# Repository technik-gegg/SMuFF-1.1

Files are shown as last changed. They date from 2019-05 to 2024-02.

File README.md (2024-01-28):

# Welcome to the SMuFF project

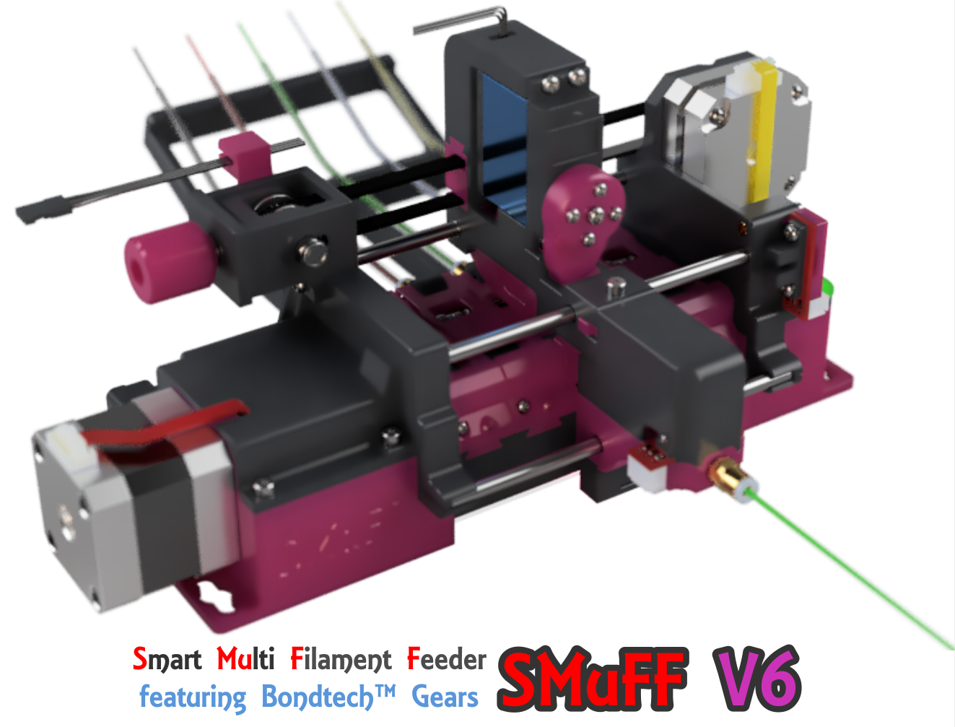
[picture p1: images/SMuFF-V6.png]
The SMuFF


Here's the official firmware package for the **S**mart **Mu**lti **F**ilament **F**eeder, as published on [Printables](https://www.printables.com/de/model/194737-smuff-v6-smart-multi-filament-feeder-with-bondtech) and [Thingiverse](https://www.thingiverse.com/thing:3431438). Read the full story on how it came to life on my official [SMuFF homepage](https://sites.google.com/view/the-smuff/).

If you like this project and find it useful, you may consider [donating](https://sites.google.com/view/the-smuff/downloads/assembly-manual#h.m5ewgcp0jfk6).

To use this firmware, you have to [compile it](https://sites.google.com/view/the-smuff/how-to/tutorials/compile-the-firmware?authuser=0) and flash it to one of these (already supported) controller boards:

| Board |  |
|---|-----|
| Bigtreetech [SKR mini E3 V3.0](https://www.biqu.equipment/products/bigtreetech-skr-mini-e3-v2-0-32-bit-control-board-for-ender-3) |**recommended** |
| Bigtreetech [SKR mini E3-DIP V1.1](https://www.biqu.equipment/products/bigtreetech-skr-e3-dip-v1-0-motherboard-for-ender-3)||
| Bigtreetech [SKR mini E3 V2.0](https://www.biqu.equipment/products/bigtreetech-skr-mini-e3-v2-0-32-bit-control-board-integrated-tmc2209-uart-for-ender-4) ||
| Bigtreetech [SKR mini V1.1](https://www.biqu.equipment/collections/control-board/products/bigtreetech-skr-mini-v1-1-motherboard-32-bit-arm-equipped-with-tmc2208-v2-1-tmc2130-spi-driver-stepstic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)||

The Bigtreetech SKR mini series boards are very small and yet powerful because of the 32-Bit STM Microcontroller Unit.

Of course, this firmware can also be configured to run on any other controller board, as long as it meets the specifications. Although you might be able to utilize older 8 bit boards, I don't recommended it - you'll most probably run out of memory (Flash/RAM) very soon. I recommend using a 32 bit controller board instead.
Make sure your board of choice has at least **256K** of Flash memory, **48K** of (S)RAM and all other components needed, which are at least:

+ two stepper motor drivers (sockets)
+ two endstop connectors
+ one servo connector (or two spare I/O pins for Software-I2C)
+ an onboard SD-Card
+ one spare serial port (USB or TTL)
+ a 128 x 64 pixel display connector
+ a rotary encoder connector

Simply create a new build environment in your **platformio.ini** and adopt the settings according to your controllers hardware in your custom **pins.h** file.

The configuration files **\*.json** and **debug.txt** have to be copied into the root folder of your SD-Card for the controller board. Hence, changing runtime parameters doesn't require recompiling the firmware. Just edit the settings from within the built-in menus or the [WebInterface](https://github.com/technik-gegg/SMuFF-WI), save them and reboot.

I've added the option to run GCode scripts for automated testing of your hardware.
In the **test** folder you'll find some sample scripts. Copy the folder over to your SD-Card and pick a script from within the menu to start the test run. Once started, the test will run infinitelly until you stop it.
Each test result will be displayed on the LCD and also sent to the log serial port (which is the USB port, if not defined otherwise).

For more information about building the SMuFF and some more detailed stuff, head over to my official [SMuFF homepage](https://sites.google.com/view/the-smuff/) or to my [Discord server](https://discord.com/invite/BzZ3rBf).

 

---

## Credit where credit is due

A special thanks to the folks who have created the following (Arduino) libraries, on which the SMuFF firmware builds upon:

+ [Adafruit](https://github.com/technik-gegg/Adafruit-PWM-Servo-Driver-Library.git) for the PWM Servo library
+ [Benoît Blanchon](https://github.com/bblanchon/ArduinoJson.git) for the Arduino JSON library
+ [Bill Greinman](https://github.com/greiman/SdFat) for the SD-Card library
+ [Oliver Kraus](https://github.com/olikraus/U8G2_Arduino.git) for the U8G2 display library
+ [teemuatlut](https://github.com/teemuatlut/TMCStepper) for the TMC-Stepper library
+ [the creators of the](https://github.com/technik-gegg/SoftWireSTM32/) SoftWireSTM32 library
+ [Tom Schimansky](https://github.com/TomSchimansky/CustomTkinter) for the Custom Tkinter Python package
+ [Akash Bora](https://github.com/Akascape) for the CTkMessagebox and CTkToolTip packages

---

## Recent changes

**3.25** - minor fixes/changes

+ restricted scanning of the I2C bus to valid slave addresses (0-7 and 120-127 are reserved addresses). Although this didn't cause any error yet, it could have caused some unwanted effects in the future.
+ added a new option to route debug messages to other than the default Serial 2 (a.k.a. TFT-Header): Create a file in the root folder of the SD-Card named:
  + **dbg2usb.txt** for Serial 0 (a.k.a. USB)
  + **dbg2exp.txt** for Serial 1
  + **dbg2oth.txt** for Serial 3

   **Keep in mind:** These files need no content. Not every port (except USB) is available on every board, it depends on board and configuration. To reset sending debug messages to default Serial 2, delete or rename the file.
+ added the **Adafruit Stepper + DC Motor FeatherWing** board as a 2nd option for the Spool-Rewinder controller. To use it, you have to define **USE_SPOOLMOTOR_FEATHERWING** in addition to **USE_SPOOLMOTOR** in the *config_defaults* and/or tick the according option in the *Firmware Build Configurator*.

**3.24** - added new "Firmware-Build Configurator"

+ made the build configuration easier by adding a custom dialog (Python/Ctk). Now, the *PROJECT TASKS* treeview only contains the basic build environments for each supported controller. Everything else can now be configured right after clicking on the **Build** task using this dialog:
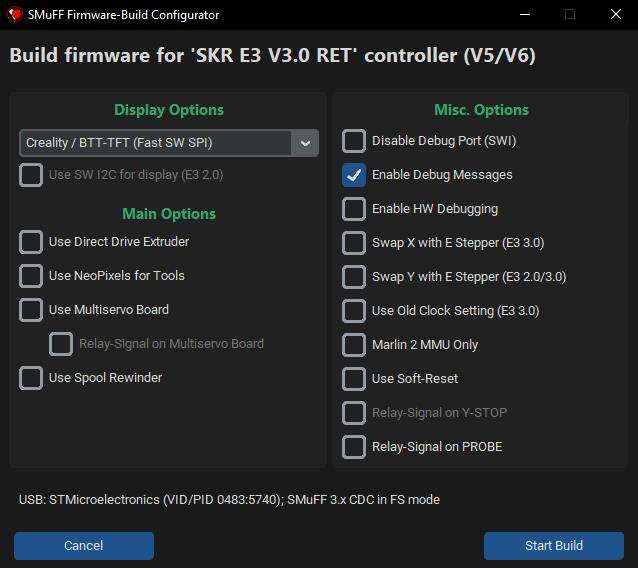
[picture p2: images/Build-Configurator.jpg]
Firmware Build Configurator

This is by far more convenient than parsing through the *platformio.ini* or trying to find the build environment you want.
Tooltips will show up when hovering over the checkboxes, which briefly explain why you would use this option.
After the build you'll find a **readme-build.txt** file in the output folder, listing the options that have been set for this particular build.
To define a set of **personalized default settings** depending on the controller used, one can list them under the *config_defaults* section in *platformio.ini*.
*Please be aware that for using this feature, PlatformIO needs to install some Python packages once. This happens automatically at your very first build.*
+ updated SdFat library reference to 2.2.0
+ added the option to use the "old" clock settings (those recommended by STM) for the SKR E3 V3.0 board instead of the new ones introduced in version 3.23.
+ added a couple more debug messages while the firmware is being initialized.

**3.23** - bugfix, Motorized Spool Rewinder option added

+ fixed the bug that caused some (newer) SKR E3 V3.0 boards not being recognized (enumerated) when connected via USB.
+ added **_SPM** build environments, which allow utilizing the [Motorized Spool Rewinder](https://sites.google.com/view/the-smuff/how-to/build/the-spool-rewinder). To use this option, you have to copy the *help* and *menus* folders to your SMuFFs SD-Card. Also, please notice the added content in **MATERIALS.json**.
+ added GCodes **M3**, **M4** and **M5** to allow controlling the spool motors of the *Motorized Spool Rewinder*.

**3.22** - reorganized Build Environments

+ reorganized Build Environments as announced in 3.21.
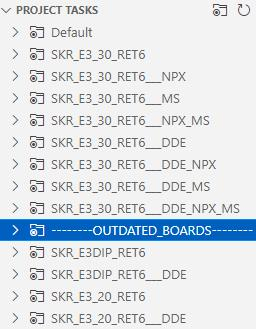
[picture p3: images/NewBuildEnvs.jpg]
New Build Environments
.
+ added include of <stdint.h> to SMuFF.h, since latest builds seem to fail.

**3.21** - some changes based on the previous release

+ reworked the Build Environments in **platformio.ini**
 Since the **SKR E3 V3.0** has become the most dominant contoller board and the others are getting more and more outdated, I've decided to get rid of some of the Build Environments for "older boards" and add all the possible permutations for the E3 V3.0 instead. The suffixes are meant to be self-explanatory but as a hint: **NPX** means NeoPixels (on tools), **MS** means Multiservo and **DDE** means Direct Drive Extruder.
 Here's what the *PROJECT TASKS* treeview in VSCode now looks like:
 New Build Environments
 Simply open the Build Enviroment that matches your setup and click on "Build".
 Outdated Build Environments are still contained in the ini-file but need to be un-commented in order to make them show up in the *PROJECT TASKS* treeview.
+ the (FYSECT / BTT / MKS) **MiniPanel 12864 V2.1** display has become the default option now. It's the cheapest and easiest to source display, so I declared it the "standard".
+ while playing around with the new behaviour of **USE_NUM_PIXELS** introduced in the previous release, I figured, it's far easier to have the number of LEDs configurable at runtime and thus, I've moved it to the SMuFF configuration file. Hence, this definition is now gone from the platformio.ini!
When you update to this version, please keep in mind to also copy the new **display.mnu** and **m205.txt** to your SMuFF's SD-Card, into the folders *menu* and *help* accordingly.
+ I also found an unpleasant but logical behavior in the *Marquee* animation when more than 7 LEDs are in use: It skips LEDs because on the beatsin() calculation and BPM settings, so I fixed that.
+ while I was at it, I also added two new Idle-Animations: Rainbow and Cylone. Thus, you need to copy the **anim-type.opt** to the *options* folder as well. Then pick the one that you fancy the most from the *Display menu*.

**3.20** - small feature change

+ corrected the behaviour of the **USE_NUM_PIXELS** definition in *platformio.ini*. This defines how many **NeoPixel LEDs** one plans to use for one tool (which usually is: "1 LED per tool").
This feature comes in handy when you're using a NeoPixel strip with a higher density. The "standard" NeoPixel strips come with a density of 60 LEDs/meter but they're also available in 30, 72, 96, 144, 240 or even 332 LEDs/m.
It turned out, that on strips with **144 LEDs/m** the LED spacing is around 7mm (i.e. 1000/144 = 6.94), which corresponds to 3 LEDs for 21mm! Coincidentally, this is also the exact width of one Filament-Guide. Hence, using a 144 LED/m strip saves you from the tedious job of cutting a strip and re-soldering the LEDs in order to get them into the right position. Simply use a longer strip (3 LEDs * number_of_tools) and set **USE_NUM_PIXELS** to 3 before compiling the firmware.

**3.19** - bug fix

+ fixed bug in Selector homing. When homed, SMuFF wasn't able to select tools because the Selector endstop was still triggering.

**3.18** - minor bug fix

+ fixed bug in displaying menu items

**3.17** - minor bug fixes / optimizations

+ fixed bug in platformio.ini for SKR Mini environment.
+ fixed bug in *NeoPixels on Tools*, if more than 5 tools are being used. Init of the NeoPixels happened before the Config was read and hence the count of tools/NeoPixels was incorrect.
+ optimized code for the steppers (*ZStepperLib*) yet again. The *isrStepperTimerHandler()* method now has an overall runtime of about **15uS** on a **STM32F1** MCU running at 72MHz.
+ changed some methods in timers.h/timers.cpp in order to shave off some microseconds in processing time.
+ fixed bug in synchronous movement of the steppers. Feeder stepper wasn't moving at the same pace as the DDE Feeder.
+ changed the USB signature to **STMicroelectronics SMuFF 3.x**. This way it's easier to distinguish which controller is for the SMuFF on the Raspberry Pi.
+ added meaningfull description headers to all methods in *ZStepperLib*, so it can be reused in other projects.
+ moved hardware Debug-Pin for E3-DIP controller from **Y-STOP** to **SWCLK** for a cleaner wave form. Since this is for my debugging only, you don't have to care much about this change.
+ removed TMC library and build flags from **E3-DIP** and **SKR MINI**, since those boards have no native TMC support (i.e. not being controlled through serial or SPI) and hence TMC drivers are running in "Standalone" a.k.a. "A4988" mode.
+ modified the **Acceleration Distance** behaviour. If this value is set to **0**, SMuFF will use 20% of the total distance for accel/decel, which results in a somewhat smoother acceleration/deceleration.
+ fixed bug stepper movement not stopping on endstop trigger. For some (still undiscovered) reason, the endstop ISR doesn't fire while steppers are moving.
+ changed/removed a couple of debug messages to make them a bit more meaningful.

**3.16** - bug fixes / enhancements / cleanup

+ **changed the stepper motors timer prescaler from 24Mhz to 2MHz** (internally 4MHz). This means, you **must** adjust your stepper ticks, otherwise steppers are going to turn terribly slow! Had to do this in order to gain more granular control over the stepper motors at lower speeds.
*Rule of thumb: Divide your current speed settings (Max. speed, Accel. speed, Purge speed, etc.) roughly by 10.*
The stepper timer in fact is running on double the frequency (4MHz) in order to achieve a longer pulse on the stepper driver, because now every 1st tick is used to set the STEP signal, every 2nd to reset the STEP signal. This makes the *Step-Delay* setting unnecessary and you should set it to 0. Though I left this setting in the config, just in case one needs it.
+ changed behaviour of "Unload retraction". If a value is set, it will only be executed if filament is fully loaded (down to nozzle). Keep in mind that this feature is used to shorten the filament remains when using the Cutter and yet only works on a Bowden setup.
+ changed data-type in *purgeFilament()* from uint16_t to double for more accurate purging.
+ changed the method of debug outputs in endstop interrupt functions, since sending data to serial ports from within ISR routines is always a bit critical and may block or crash the controller.
+ added **DEV4** debug flag for a more granular output control of debug messages (i.e. printing incoming GCodes, memory stats, ...).
+ updated GCode **M100** to determine free system memory (RAM). Before, this GCode only returned "ok".
+ added printing out memory stats every minute if *DEV4* debug flag is set.
+ removed the "*Mirroring the display on a VT-100 terminal*" feature introduced in V2.24 completely. Although it was nice to have back then, the software options around the SMuFF have evolved. Hence this feature is obsolete now and was only messing up the source code.
+ removed the (meanwhile) obsolete conditional code for FastLED library. My modified Adafruit NeoPixel library is covering all that's needed.
+ overhauled the code for handling the NeoPixels on tools. NeoPixels will not update as long as one of the stepper motors is spinning (Feeder / Selector), which makes the steppers run smoother.
+ added parameter **P** to GCode **M700** (load filament) in order to purge material (after it's being loaded). If no *value* (e.g. *M700 P*) is given, it'll purge the configured purge amount, otherwise the length of filament given in *value* (e.g. *M700 P12.34*).

  **[ Bug fixes ]**

+ fixed the bug that puts a "loading" dialog on the display while in *Testrun mode* (kudos to **palkovnik807**).
+ fixed the bug where retries were not being decremented while unloading filament (a.k.a "infinite loop" if unloading went wrong).
+ fixed a potential buffer overflow in *drawPurgingMessage()* and *printPeriodicalState()* functions.
+ fixed a bug that may have caused the MS1/MS2/MS3 pins being set up wrong on the **E3-DIP V1.1** (only), because the according pins on the MCU were in an undefined state. Now those pins are being set to LOW (0V) at startup.

**3.15** - minor changes / bug fixes

+ added option **NEVER_DISABLE_SERVOS** in *platformio.ini* section *'other'* which will inhibit disabling servos after they had been moved. The default behaviour is that the SMuFF will disable the PWM signal on **Wiper** and **Cutter** servos after wiping/cutting, because some servos run less jittery when disabled.
However, it turned out that disabling the PWM signal on some servos causes those servos eventually start moving out of the blue. Allowing the PWM signal to stay active helped fixing this issue.
If you discover random movements on your Wiper/Cutter servo, activate this new option before compiling the firmware.
*This option however doesn't influence the behaviour on the Multiservo board(s) - which still are the better option for driving servos.*
+ fixed the bug that sometimes caused the filament not being fully retracted (i.e. Feeder endstop not triggered). Happens only if the configured "Bowden length" value doesn't match the real distance or the filament "slipped" during retraction. In such case the Feeder was supposed to retry until the endstop has triggered but didn't due to wrong condition checking. Thanks to **palkovnik807** on Discord for pointing it out.
+ fixed the bug that caused the **DDE Feeder** not doing a purge under certain conditions because the stepper wasn't enabled. Thanks to **Thyom** on Discord for finding it.
+ added printout of DDE Feeder endstop state for GCode **M119**, in case SMuFF is configured for DDE.

**3.14** - minor changes / bug fix

+ added option **USE_NUM_PIXELS** in *platformio.ini*. Usually, the number of Neopixels matches the number of tools but in some special case you may have more Neopixels on your strip then tools. In order to make the animations using all pixels, enable this definition and set its value to the according number.
+ fixed bug where Lid servo didn't close before unloading when Cutter has been configured as sitting "on top".

**3.13** - Changes for Duet3D and Serial display / some bugfixes

+ fixed bug in TMC driver **Stealth-Mode setting** via SMuFF-WI. Value was accidentally inverted.
+ fixed bug that caused a compilation failure when using the *SKR_E3_30_RET6___DDE* build environment.
+ added [SMuFF-Backbone](https://sites.google.com/view/the-smuff/work-in-progress?authuser=0#h.m19pbkoy3v6p) schematic and PCB design.
+ added **DuetSerial** (port) setting to **SMUFF.json** and menus. You **must** now define the serial port where the Duet3D/RRF is connected to (set to Ser.1 by default). This serial port will only be taken into account if the SMuFF is configured for Duet3D/RRF. For this option you need to copy the modified **options.mnu** and **duet3d.opt** files into the according folders on your SMuFFs SD-Card.
+ added **DspSerial** (port) setting to **SMUFF.json**. The Display serial port can only be configured either through the **-D DISPLAY_SERIAL_PORT** definition in *platformio.ini* or manually in SMUFF.json but not from the menus (because there will be no menus in this mode). See notes on **USE_SERIAL_DISPLAY** for version **3.00** down below.
+ updated **M42** & **M280** & **M205** help files (for Multiservo use).
+ added Dialogs and Sound support on SMuFF-WI when *USE_DISPLAY_SERIAL* is enabled.
+ added **SWAP_SELECTOR_ENDSTOP** build option for those who experience the X-STOP (used for Selector) is not being triggered on a **SKR E3 V3.0**. With this option enabled, the firmware expects the Selector endstop to be connected to *Y-STOP* rather than *X-STOP*.
+ added *JAM* flag in periodical status messages; This is being used in my OctoPrint/Klipper plugins to indicate whether or not the tool change has failed for some reason.
+ added option to switch the *Debugger Serial Port* from within **debug.txt** on startup, without the need for recompiling the firmware. To use this option simply add a **;x** after the value, whereas *x* determines a port number between **0** and **3**. Port **0** always indicates the **USB** serial port, whereas ports **1..3** depend on the controller board you're using (*port 2 is the default value and is assigned to the **TFT** header on most boards*).
*Keep in mind:* This setting will vanish once you set the debug flags via GCode **M111** and store them using **M500**.
+ added option to switch the *Debugger Serial Port* on the fly via **M205** GCode. To use it, simply apply parameters **P"ChangeDbg" Sx**, whereas *x* is the number of the new serial port in the range of **0..3** (see description above).
*Keep in mind:* This setting is temporary and will be reset at the next boot.
+ added option to filter in help files. After the **?** append the phrase to filter for. For example: **M205?dist** will only show the header and all lines containing the string *"dist"*.

**3.12** - Changes for the MULTISERVO option

+ reworked **MULTISERVO** option. For one it's now named *USE_MULTISERVO* for more consistency throughout the other options. For the other, it's now being used to configure all servos to control them via an external board (Adafruit Multiservo/FeatherWing/ [SMuFF-Backbone](https://sites.google.com/view/the-smuff/work-in-progress?authuser=0#h.m19pbkoy3v6p) board). This external board is always being controlled by using software I2C. The pins used for SW-I2C vary throughout the different controller boards.
+ the **USE_MULTISERVO** flag will become more importance in the future, hence I moved that option to the *[other]* section of *platformio.ini*.
+ modified the external **SoftWireSTM32 library** which had a bug that caused that the library wasn't able to scan for devices on the I2C bus properly.
+ moved relay control pin on **SKR mini E3-DIP V1.1** from **MS3** pin of the Z-Axis driver socket (in DDE mode) to the **TH0** pin if the **USE_MULTISERVO** flag is set. This is because this signal is being used as the data pin (SDA) for the software I2C controlling the Adafruit Multiservo board.
+ added **USE_MULTISERVO_RELAY** flag to the compile options in order to control the relay via output #5 on the Multiservo board instead of *MS3*, *TH0* or *PROBE* pins. This will be the future method of controlling the relay switch. **Please notice:** This method requires a pull-up resistor of 4.7K - 10K, either on +5V or +3.3V to make the signal switch as intended. The reason being is that the outputs on the Multiservo board are configured as open-drain.
+ corrected build environment for **SKR mini V1.1** (FastLED library was still referenced instead of the Adafruit Neopixel library).
+ fixed the bug that caused the **SKR mini V1.1** to hang at startup (wrong *debugSerial* port has been initialized).
+ added a couple more meaningful error messages to the GCode interpreter.
+ changed **SERVOMAP.json** config file to reflect the new MUTISERVO options. Please copy this file over to your SMuFF's SD-Card.
+ changed **ServoMinPwm** and **ServoMaxPwm** settings in SMUFF.json. These settings work better with the Multiservo boards. Copy the modified file over to your SMuFF's SD-Card and don't forget to reconfigure your servo angle settings.
+ added the two user controlled servo ports (USER1/USER2) to **M280** GCode and **M42** GCode when using the MULTISERVO option. Send M280 P1000 / P1001 if those ports are supposed to drive custom servos, or M42 P1000 / P1001 if those ports are configured to be used as output pins (i.e. to be switched on/off).
+ added **M260** GCode to allow scanning for I2C devices at runtime using the GCode interface.
+ updated some of the KiCad files to KiCad version 6.x

**3.11** - Some minor changes

+ added flashing of the "Periodical State sending" glyph on the display when it's enabled. Flashing happens at half the frequency of states being sent.
+ added current relay state (**E** / **I**) to "Periodical States".
+ changed output of **M122W** and **M503W**. *M122W9* and *M503W0* are now sending all state/configuration data at once, which makes SMuFF-WI connect faster.

**3.10** - Some minor changes / bug fixes

+ **removed SKR E3 V1.2** from the list of supported devices because this board isn't optimal for the SMuFF V6. Consider moving to E3 V2.0 or better E3 V3.0.
+ changed some default settings in *SMUFF.json* which fits better for V6 default configuration.
+ switched from FastLED to AdafruitNeoPixel library throughout for all boards.
+ fixed bug where DDE extruder wasn't reading out the endstop while retracting.
+ fixed bug with NeoPixel refresh.
+ added dedicated timer for NeoPixel refresh because the existing solution interfered with servos and steppers.
+ (re-) added timer for servos because the existing solution interfered with the stepper timer.
+ changed timer priorities and intervals to get rid of servo jitter.
+ changed priority on timers, so the stepper timer (and thus the stepper movement) is a bit more agile now.
+ added GCode command **M155** for fast switching of *sending periodical status messages*.
+ GCode **M205 help file** updated.
+ cleaned up *platformio.ini* by extending environments in *__DDE.
+ added GCode command **M562** to reset a *Feeder Jam* remotly.
+ added more status/error responses in order to make the Klipper module run smooth
+ added feeder states (SPL in periodical states) for all variants. This value is now (lower nibble: Splitter, upper nibble: non-Splitter):
  + 0x00 means *not loaded*
  + 0x01 means *loaded to Splitter*
  + 0x02 means *loaded to Nozzle*
  + 0x10 means *loaded to Selector*
  + 0x20 means *loaded to Nozzle*
  + 0x40 means *loaded to DDE*
+ added "JAMMED" state on display when feeder is being jammed

**3.00** - Moving from Maple to Arduino Core STM32 framework  

+ ported firmware from **Maple** to new **Arduino Core STM32** (stm32duino) framework in order to make boards with different MCUs available. This version is still compatible with the predecessor SKR controller boards, such as the SKR Mini/E3-DIP/V2.0.
+ added **debug.txt** to define the amount of debug messages being spit out without re-compiling the firmware. Also added the option of changing the debug level through GCode, which is **M111**. See *M111?* for details.
+ compiling the firmware without the **-D DEBUG** option will now reduce the memory footprint drastically. Although, removing debug messages completely will make your first setup much harder, so handle with care.
+ updated help files in *help* folder.
+ reduced the number of build environments in *platformio.ini*. Please note that **USE_DUET3D** has become obsolete and is now a runtime option. However, the **USE_DDE** flag still is the same and hence it's got its own build environment (*\*___DDE*).
+ added build options summary when compiling. This makes checking the build options you've set a breeze:
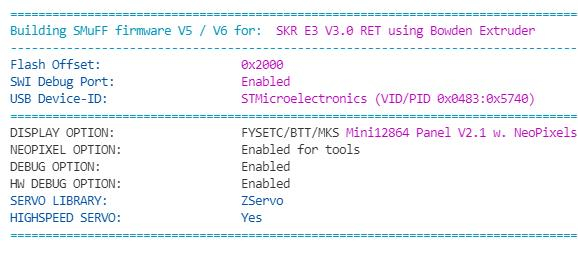
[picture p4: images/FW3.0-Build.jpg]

+ removed Servo-Timer. Servos are now served through the *General Purpose Timer*, which makes the servo timing more percise and thus the servos less jittery.
+ added flag **MIMIC_LIBMAPLE_USB_ID** in order to keep the USB ID compatible for use with my [OctoPrint plugin](https://github.com/technik-gegg/OctoPrint-Smuff). This setting is default for the "old" SKR E3 controller boards but not for newer boards.
+ added flag **SWAP_SERVOS** which will assign the Lid and the Cutter servos to the BL-Touch header for SKR E3 V1.2 / V2.0 / V3.0 (it swaps Wiper and Cutter servo signal pins).
+ added new build environment for **SKR E3 V3.0** controller board. This board has been fully tested and is ready to use.
+ added new build environment for **SKR E3 RRF** controller board. **Not tested yet!**
+ added **SyncSteppers** flag in SMUFF.json, which, if turned on, synchronizes movement of two or more steppers, so that they start and finish at the same time. Set by default.
+ eliminated code for *ZPortExpander* completely.
+ restructured **Options** menu on the display. Copy the new *options.mnu* file to the SMuFFs SD-Card (folder menus).
+ added **USE_SERIAL_DISPLAY** option for future use. ***Please be aware:** By setting this flag, no display code will be compiled into the firmware and hence the only way to control it is by using the WebInterface.*
+ added **USE_FAST_SW_SPI** build option for Creality  displays (or compatibles such as the BTT TFT). This allows you to simply connect the display through EXP1/EXP3 with the applied 10 pin cable, and still get a decent speed and responsiveness on the display.
+ added a couple of new STL files for Inlet-Guides and new SKR housing. Inlet-Guides are now available for 5 and 7 materials (thanks to maker **Defenc**). For a different amount of materials on the Inlet-Guides, please download the according [STEP file from Thangs](https://thangs.com/mythangs/file/55305).
+ fixed bug which caused the SMuFF to hang after showing the main menu.
+ refactored some code from **SMuFFtools.cpp** into *DisplayTools.cpp*, *SoundTools.cpp* *ServoTools.cpp* and *TerminalTools.cpp* for better maintainability.

---

**2.44** - Addition for alternative RRF boards

+ added inverting option for the *Busy* signal that goes to a endstop of a RepRap Firmware board (other than the Duet3D). This was needed since some of the alternatives might not be able to trigger upon the original signal. To use this option, you'll also need to copy the updated **options.mnu** file to the *menus* folder of your SMuFFs SD-Card.
Basic instructions for setting up a RRF (Duet3D) board can be found [here](https://sites.google.com/view/the-smuff/how-to/tutorials/configure-the-duet3d?authuser=0).
+ removed old code that might have disturbed Duet3D signals.
+ fixed a typo in the folder name which caused the E3 V1.2 version not being able to build correctly.
+ reorganized *Build Environments* in platformio.ini. This change allows you to pick some of the build options quickly. In the *Project Tasks* you'll now find different environments named after the controller board (i.e. **SKR_E3_12** for the SKR E3 Version 1.2) and three with the same name plus an extension named either **DDE**, **DUET** or **DDE+DUET**. The one without an extension is the "basic" version (no DDE, no Duet3D). **DDE** builds the firmware for the DDE option, **DUET** for the Duet3D (a.k.a. RRF) and **DDE+DUET** for a combination of both of the previously mentioned options. Thus, you don't have to mess with these settings in the [options] / [extruder] section anymore (the latter section has become obsolete now).
Keep in mind that you still have to set the correct **display** option before you build the firmware, in case you're using something else than the DIY display.
+ added **M118** GCode to enable you to send text (GCode) from the SMuFF/WI console to a specific serial port. Parameters are the same as for Duet3D/RRF fimrware, whereas **P**x defines the serial port, and **S**"..." defines the message to send. Please update you *help* folder with the latest files.

**2.43** - added new STLs

+ added new STL files for the small servo carrier. Please read [the instructions posted here](https://sites.google.com/view/the-smuff/work-in-progress?authuser=0#h.ssx9ayceh6f4).
+ updated version number to make the version check in WebInterface happy again.

**2.42** - some minor bug fixes/changes

+ made contrast setting a live function (contrast of the display will change as you rotate the knob, which makes it easier to set up).
+ corrected contrast setting after reading configuration on startup.
+ changed backlight color order on *FYSETC Minipanel* from GRB to RGB.
+ added SKR E3 RRF board to the collection. **This is experimental only and will not compile due to the lack of support for STM32F4 in some libraries. Do not use!**

**2.41** - some fine tuning on recent changes

+ added **DebugFreq** setting to **SMUFF.json** which allows to set the frequency (in Hz) applied to the hardware debug pin for testing purposes. This value can be changed during runtime via M205 GCode as well.
+ defined Duet3D signal pins (*DUET_SIG_FED_PIN* and *DUET_SIG_SEL_PIN*) to be on thermistor pins (THB and TH0). Because of the R/C filter on those pins signals are limited to a max. switching frequency of **100Hz**, which is sufficient for this purpose.
+ removed redundancy in display includes throughout all the Pins.h files. These are now located once in *Display/Display.h*.
+ corrected some pin defintions in all Pins.h files.
+ revived the SKR Mini V1.1 board (because it's still available and in use).

**2.40** - code reorganization and bug fixing

+ removed old boards, such as ESP32, SKR Mini, FYSETC AIO II, mainly because they're discontinued and just mess up the project.
*Because of this change the version number is now 2.4*
+ removed code for ESP32 entirely. As long as the ESP32 has such a deficit on I/O pins, it's not feasible as a SMuFF controller.
+ split up **Pins.h** to disentangle the confusing code for display pin definitions. Now each display type has it's own *DSP_xxx.h* header file and the initialization takes place in the according *Display/xxx.h* file instead of *SMuFF.cpp* and *SMuFF.h*.
+ reorganized code in order to reduce memory footprint and allow compiling for NeoPixels unconditionally. Due to usage of the PortExpander (PCF857X), which only purpose was to extend the amount of I/O ports on the ESP32, the memory footprint exploded. It's corrected now and the memory (RAM) footprint is slightly around 35% instead of 86%!
+ corrected pinout for standard RepRap display and FYSETC 12864 Minipanel on E3 V2.0 board.
+ improved drawing speed on the DIY OLED display for E3 V2.0 board.

**2.34 - 2.39** - skipped versions

**2.33** - bug fixing for DDE option

+ fixed a bug that caused stalling on the DDE stepper motor while purging because of wrong settings.
+ added more frequent status information for the WebInterface while swapping tools.

**2.32** - added Cutter position for DDE option

+ **moved main repository on Github to SMuFF-2.0 branch. No need to download from the SMuFF-2.0-(Experimental) anymore.**
+ added **CutterTop** option in SMUFF.json which was needed for the latest Orbiter-Extruder mod. For the Orbiter-Extruder you need to set this option to *false* because the Cutter sits below the DDE.

**2.31** - added Cutter handling for DDE option

+ added purging of filament when DDE is being used in conjunction with the Cutter in order to release the 2nd endstop. To use this, set the **PurgeDDE** flag in SMUFF.json accordingly.
+ fixed bug in feedToEndstop which caused an abort if the *InsLen* parameter was set too low.
+ added all **STL files** for V6 to this repository
+ added **Device** parameter in SMUFF.json. This string can be 15 charaters long and sets a distinct name for the current SMuFF device (i.e. the printer it is attached to). The name of the device will be show up in the WebInterface and also in GCode **M503**. This name can only be set/changed through the WebInterface or directly in the config file but not in the menu.

**2.30** - DDE option added

+ added **USE_DDE** flag in platformio.ini. Set this flag if you intend using the SMuFF on a Direct Drive Extruder. Further instructions you'll find on the [SMuFFs website](https://sites.google.com/view/the-smuff/how-to/tutorials/set-up-a-dde).
+ added new menu items in **options** menu for DDE. *Please notice:* The Use DDE flag can't be switched during runtime, it's only shown to indicate whether ot not this firmware was compiled for DDE.

**2.29** - Some critical changes, Splitter option added

+ **Critical:** Moved pin for **switching the relay** from *PROBE* to the *MS3* pin of the Z-Axis stepper driver for E3-DIP boards. This was needed since the PROBE pin sometimes has a problem delivering a valid signal for the relay board. If you still encounter problems switching the relay, try adding a 10K pull-ip resistor between +5V and the signal pin MS3.
+ added some minor changes to improve the communication with the [WebInterface](https://github.com/technik-gegg/SMuFF-WI).
+ fully integrated the Splitter option.
+ added new **main-menu** variant for the Splitter option.
+ added Splitter option settings in **options** menu.
+ extended **M700** and **M701** GCodes to handle Splitter option. A suffix **S** loads unloads to/from Splitter, whereas a  **R** suffix in M701 allows you to reset the currently saved states.
+ added feed states for Splitter option, which reflects if and to where the filament has been loaded. States will also get saved to EEPROM.json.
+ added new icon for the "fully loaded" state (in F2) on the main screen when using Splitter option.
+ fixed bug not turning display backlight back on after idle state.
+ set Servo min./max PWM to more conservative values of 900 and 2100. This might force you to tweak the Lid open/close positions on your SMuFF a bit. If you go below minimum and above maximum, this might cause your servo to overheat and eventually break (depends on the servo).
+ added software support for EStop MUX when using the "advanced" Splitter option. This feature is using the 2nd I2C (EN/STEP pins on Z-Axis steper driver socket) pins for communication if not compiled for the DIY/LeoNerd's display. On DIY/LeoNerd's displays it uses the 1st I2C, which also drives the display. To enable you to use this option, you'll need to compile the firmware with setting the **USE_SPLITTER_ENDSTOPS** definition in *platformio.ini*.

**2.28** - More bug fixing for WebInterface, added linear stepper support for Lid

+ fixed bug causing test GCode not being executed when initiated over [WebInterface](https://github.com/technik-gegg/SMuFF-WI).
+ added new periodical status infomration for TMC, SD-Card and LID.
+ changed the periodical status interval to 0.5 sec. when connected to the [WebInterface](https://github.com/technik-gegg/SMuFF-WI).
+ added option to compile for **V6S**, which is basically V6 but using a linear stepper on the Y-Axis (Revolver) for the Lid instead of a servo.
**Please notice:** *When using this option, the servo signals (Wiper & Cutter) come from the Z-Axis socket. Wiper signal moves to DIR pin, whereas Cutter signal moves to MS3 pin. That's because the STEP and EN pins are being used for the 3rd serial interface.*
+ added REVOLVERMAP.json to the configuration files, which defines the travel distance for the Lid linear stepper on each slot separately.
+ added materials (as in PLA, PETG, ...) to the materials definitions. Old "Materials" became "MaterialColors".
+ cleaned up code in GCode parser, saved a few bytes of Flash memory.

**2.27** - Bug fixes for WebInterface

+ corrected setting for "Speeds in mm/s".
+ corrected "Fan Speed" value validation (minimum was 1 instead of 0).
+ added synchronization with WebInterface when settings were changed locally.
+ set Heated Bed pin to 0 in init. So it won't turn on the heater MOSFET anymore.
+ fixed bug that caused the relay not switching when *useServo* was set to false.

**2.26** - Important changes

+ due to low memory on some boards, I had to split the **SMUFF.json** and relocate the steppers configuration into a separate file **STEPPERS.json**. Please make sure that you copy this new file to your SD-Card as well.
+ because of the same reason I removed the "Ser*N*Spd" setting in the SMUFF.json configuration file and replaced it for an array named "Baudrates".
+ changed **M205** GCode command and made all settings available. This way remote controlling it is way easier.
+ added some functions for the [SMuFF WebInterface](https://github.com/technik-gegg/SMuFF-WI) app.

**2.25** - Minor changes for Duet3D

+ modified the logic for interfacing with a Duet3D controller.
+ added **M577** GCode command to retrieve Duet3D signal pins status. Connection needs one additional wire from the SMuFF down to the Duet3D end stop input in order to do tool changes properly.

**2.24** - Minor changes

+ replaced all UTF characters in menus. Please copy all menu files onto your SD-Card and replace the old ones.
+ added a feature to mirror the display contents on a debug terminal (VT100 terminal emulation). This will only work on a controller board that has a *..RET..* MCU (because of the doubled memory) and if it's being enabled manually in the **SMuFF.json** config (**TermMenu** set to **true**).
**Please notice**: This feature was made for conveniance purposes (i.e. when you're connected to the debug interface having the printer/SMuFF out of sight). It's not meant to replace the display.
If this feature is turned on and when not in menus, the topmost line on teminal will replicate the information of the SMuFFs main screen.
+ corrected **Microsteps** options for TMC drivers.
+ removed I2C scanning when no IC2/TWI device is expected because the scanner is blocking the startup for a couple of seconds.
+ moved buzzer timer because it interfered with software serial library.
+ updated some help files.
+ revived loading sounds from SD-Card function. You can now modifiy all sounds to your personal flavor (see README.md within sounds folder for instructions).

**2.23** - Minor changes / bug fixes

+ added separate definitions for LED_TYPE and COLOR_ORDER for backlight and tool Neopixels.
+ changed name *servo* to *servoWiper* to avoid ambiguity.
+ changed **LED_TYPE** and **COLOR_ORDER** on **MINI12864 PANEL V2.1** because it turned out to be WS2811 not WS2812B.
+ changed **M206** to use floating point values for the Selector distance.
+ added checking for min. speed when using mm/s. Min. speed for Selector is about 5 mm/s because of the lower steps/mm. Feeder can go down as far as 1 mm/s.
+ fixed a bug in the calculation of speeds in mm/s. **However, I still recommend using speed settings in ticks rather than mm/s** (that's: SpeedsInMMs set to false). If you do use mm/s, please be aware that accelleration/decelleration are not being taken into account and therefore it's only a close estimation of the speed (which doesn't really matter for the function of the SMuFF anyway).
+ fixed bug for not initializing the software serial when not running on a SKR E3 2.0 board (which operates on a hardware serial).
+ added back setting the internal RSense on a TMC stepper driver when not on a SKR E3 1.2/2.0 board.
+ added software I2C support for LeoNerds OLED module (by GMagician). **Please notice**: If you get a compile time error stating *LeoNerdEncoder::begin(SoftWire\*)* has not been found, you have to delete the LeoNerd-OLED-Module-Library folder from the **.pio/libdeps** folder manually.

**2.22** - Changed configuration file names; Minor changes for FastLEDs

+ **IMPORTANT:** Configuration files must now have the **.json** extension, **not .CFG**! This was necessary because most people forgot to rename them and thus the SMuFF failed at startup.
*From now on, just copy the configuration files to the root of your SD-Card; no need to rename the files.*
+ updated Neopixel (FastLED) functions / animations.
+ added **Anim. BPM** and **Status BPM** settings in **Display** menu.
+ added parameter **AnimBPM** and **StatusBPM** to  M205 GCode command to allow the remote setting of the animation / status Neopixel speeds (it's **B**eats **P**er **M**inute - which you sure have guessed already).
+ added *CValue* entry to **MATERIALS.json** which defines the color to be set on the Neopixel strip for tools (has to be a 6 byte hex string i.e. "0F1C03A").
+ added parameter **C** to **M145** GCode command which accepts the same color string as mentioned above.
+ updated files in **menus** and **help** folders (make sure you copy those onto your SD-Card).
+ added **EEPROM.json** to the configuration files. Copy this along with the other **.json** files to the root of your SD-Card.
+ redesign of the main screen in order to show more information at a glance. Beside the existing informations, you'll now see the shared stepper status (**E** or **I**), the mode (**SMuFF** or **PMMU2**), whether pruging is active (**P**), whether TMC drivers are supported (**TMC**) and a warning sign (**!**) if they have reported issues and whether or not periodic status information is being turned on (**&#x27F3;** Symbol).
+ made servo movements faster due to a more realistic calculation of position setting times (based on Max. speed of 200ms per 60° - typically 70-180 ms)
+ added **InvRelay** to SMUFF.CFG and **Options** menu, in order to invert the relay switching signal if needed. Turned out that Adafruit and Velleman relay boards behave different on this topic.
+ induced error message (and compiler stop) if you try to run the LeoNerd's OLED Module via software I2C. This is the case with **E3 2.0** controller board only.

**2.21** - Minor changes / bug fixes

+ moved config files into Configs directory, since there are no specific configs for different controller boards anymore.
+ changed default speed of all serial ports to **115200** in SMUFF.CFG (which makes more sense nowadays).
+ fixed the bug that was causing stepper motors not moving when TMC2209s are being used in UART mode (which primarily affected the SKR E3 V1.2 and V2.0 boards).
+ splitted FastLED definition for BACKLIGHT and TOOLS.
+ added some FastLED code.
+ added menu entry in **Display** to define tool (LED) color when having set **USE_FASTLED_TOOLS**.
+ fixed bug that caused EEPROM.DAT not being created.
+ fixed bug that caused the main screen not to refresh after selecting a tool.
+ renamed build environments **\_E3\_SD** to **\_E3\_1.2\_SD** and **\_E3\_SD\_20** to **\_E3\_2.0\_SD** in order to make it more obvious.
+ display in Testrun mode isn't flickery anymore.
+ added a 2nd page to the status info for TMC2209 stepper drivers (uses encoder to flip between the pages).
+ case fan is now working correctly. It'll be controlled with a default frequency of 100 Hz. The frequency can be modified through *Config.h*. Make sure you have a fan with the corresponding voltage rating (same as you use to power the controller).
+ the positioning of servo angles is now more accurate (about 5 deg.; it was about 10 deg. before).

**2.20** - Minor bugfix for test scripts / Overhaul for 32-Bit only

+ GMagican kindly did some code review and removed code that was releated to the 8-Bit AVR MCUs. He also added a HAL for ESP32 MCUs (just in case for future controllers based on this MCU family).
+ fixed some outdated settings in the test scripts which caused the test scripts not running correctly (i.e. Feeder-Test).
+ added an InputDialog for 16 bit values.
+ Original SdFat from greiman version 2.x will compile now.
+ added FastLED support for tools. This one has to be enabled by setting the **USE_FASTLED_BACKLIGHT** flag and the **NEOPIXEL_TOOL_PIN**. **Using this feature may render your controller unstable if it has not enough RAM**. Newer boards such as the E3-DIP with 64KB of RAM outght to be preferred.

**2.19** - STM32 platform update / SKR E3 bug fixing / Purge added

+ updated STM32 platform to version **11.0.0**. Please do the same, since 10.0.1 seems to have a lot of issues. Also, be aware that 11.0.0 also still has bugs, i.e. the I2C bus enumeration will not report any device available! Though, devices attached work flawlessly (as far as I can tell).
+ swapped signal pins for TX on Z and E stepper driver.
+ changed **board** setting in *platformio.ini* for E3-DIP to genericSTM32F103**RE**, since newer boards come with the RET6 MCU (means: twice as much Flash and RAM). Please check the MCU on your board and set it back to genericSTM32F103**RC** if it says STM32F103**RC**T6!
+ added **PurgeSpeed** and **PurgeLen** to the configuration and menus (*Purge Control* in settings). If *PurgeLen* is set to a value greater 0 and the purge feature is enabled, the SMuFF will purge the amount given in *PurgeLen* with the given *PurgeSpeed* after the tool change. This configuration is needed because under some (so far unknown) circumstances, the OctoPrint plugin (or even the printer, not sure which one to blame) tends to hang when extrusions are being executed within the tool changing process (that is: within the **BeforeToolChange** and **AfterToolChange** scripts).
You have to figure the correct length for purging yourself. However, if you happen to know the purge volume for your filament, you can easily calculate the length by dividing the purge volume by 2.4 (for a 1.75 diameter filament this equals to: 280 mm³ / 2.4 = 116 mm). You may have to adjust this value but at least it's a good starting point.
+ modified contents of **MATERIALS.CFG**. Restructured the file contents and added *Material*, *Color* and *PFactor* settings to it.**Copy the new one onto your SD-Card**.
+ added **PFactor** setting in **MATERIALS.CFG**. This configuration file lets you define and store the purge factor (in percent) related to the initial **PurgeLen** definition. This might be useful when you experience color bleeding on lighter colors (such as white).
+ added **M145** GCode command which lets you define material colors/names and the purge factor for each material conveniently via terminal app. That's because the purge factors in the purge menu will show the tool number and material/color name. This way it's easier to determine on which to modify the purge factor.
+ fixed a bug which caused the tool change to fail when initiated via the tools menu because the lid servo didn't open correctly.
+ modified existing / added new menus (*settings.mnu*, *purge.mnu*). Copy those to the **menus folder** on your SD-Card.
+ added *UnloadRetract* to the **Purge Control** menu. This value retracts the filament the given amount before it gets cut. I did this to reduce the amount of filament that remains in the hotend and thus reduce the amount that needs to be purged at all. You're supposed to set this value to the distance between the nozzle and the cutters blade (somewhere around 50 mm for my Ender-3 Cutter design, for example).
+ added **UseEStop2** setting for the feeder. If you enable this setting, the SMuFF will check whether or not the 2nd endstop is being triggered when loading/unloading and take actions if not (also related to it is setting EStopTest, which defines the trigger state). This endstop is supposed to sit near the very end of the bowden tube (right on top of the cutter, in case you use that).
+ added **Wipe Nozzle** and **Cut Filament** to the main menu. Copy the newer main*.mnu files to your SD-Cards menu folder.
+ added a constraint for version **>=11.0.0** to the STSTM32 platform in all STM32 releated build environments (for good measure).
+ added a constraint for version **=1.1.4** to the SdFat library. This library has been updated to 2.0.0 and seems to have issues when compiling.
+ changed the default setting **SpeedsInMms** to **false**. This means, speeds are **no** longer defined in mm/s by default but in ticks. **Keep in mind:** Ticks have to go up when you want to **slow down** the stepper movement and, vice versa, decrement if you want to speed the motion up. The SMUFF.CFG contains some conservative values for you to begin with. Using ticks instead of mm/s makes controlling the motion of the stepper motors much more fine tuneable.

**2.18** - SKR E3 V2.0 bug fixing

+ changed the way how the TMC steppers are being initilized using HW serial (important for SKR E3 V2 only).
+ fixed the TWI/I2C OLED display. Instead of hardware I2C, as I mistakenly mentioned earlier, it now uses software I2C since the according pins for hardware I2C (PB6/PB7) are not routed to the EXP1 header but to the additional EEPROM. This makes the display noticeably slower but useable. To speed up the display, you'll need a display that utilizes SPI and the according mod as added in 2.15 [and mentioned here](https://sites.google.com/view/the-smuff/tips-hints/using-other-displays).

**2.17** - minor modifications

+ added parsing for "**\n**" (two bytes) in the received data, which eventually gets threated as line-feed ('**_\n_**'). This is needed for Duet3D / RRF firmware which doesn't send a LF at the end of a message when sent using **M118** GCode.
+ added Filament-Cutter handling (see [Filament-Cutter](https://www.thingiverse.com/thing:4650129)). Be aware that you'll need to attach the servo to **SERVO3_PIN**, which is not available on all controller boards. For those board which support only two servos, you have to pick either Wiper **or** Cutter and assign it accordingly in the *Pins.h* file. Usage of the cutter and open/close positions are defined through the **Options** menu (SMUFF.CFG).
Cutting filament can also be activated through the **G12 C** GCode command. Because of this change, the files **options.mnu** and **g12.txt** have changed and must be copied to the SD-Card, as well as the SMUFF.CFG.
+ added function keys (PF1-PF4) to be used in VT100 terminal emulation which will execute the commands assigned in *LBtnDown*, *LBtnHold*, *RBtnDown* and *RBtnHold* accordingly.
**Please notice:** The PF1-PF4 keys in the terminal emulator are not assigned to F1-F4 but are located on the upper row of the NUM-Pad ('Num-Lock', '/', '*', '-' keys) in **TeraTerm**.

**2.16** - framework update

+ updated to STM32 framework V10.0.1 and though needed some code changes in various files (mostly related to SdFs library modifications). Please make sure you have updated your platformio STM32 framework to that version.
+ changed to a different SdFs library in platformio.ini
+ fixed bug in getFiles() which prevented getting a full list of files if a different extenstion was found (i.e. '.md')
+ changed \__debug() to \__debugS() since it conflicted whith some new namespace defined in latest framework
+ added -D ARDUINO_ARCH_STM32 to all STM32 build environments. This is needed because otherwise the TMCStepper library will not compile correctly and the SMuFF will hang at startup if you compile for TMC2209s!

**2.15** - minor changes

+ added a "D" to the version number if the firmware has been compiled in DEBUG mode. This might be useful since some 3D printer firmwares don't like it much if you send unexpected data and decide to go bonkers.
+ corrected standard RepRap Full Graphics Display driver
+ added CREALITY_HW_SPI compile flag in order to be used with [this tweak](https://sites.google.com/view/the-smuff/tips-hints/using-other-displays?authuser=0)

**2.14** - yet another bug fixing seesion

+ **Attention:** Renamed almost all parameters in SMUFF.CFG and TMCDRVR.CFG because of memory issues. Don't use your existing ones but rather copy the new files from this repository to your SD-Card
+ increased memory allocation for config files (reading TMCDRVR.CFG failed)
+ removed scanning for I2C devices when not using any I2C components (USE_CREALITY_DISPLAY will fail because of this)
+ updated code for Multiservo
+ corrected colors for RGB backlit displays
+ re-enabled remapping of SPI3/1 in case it's needed (via STM32_REMAP_SPI flag)
+ enabled all __debug() messages in setup() for easier troubleshooting. Once your SMuFF is starting up correctly, recompile firmware without DEGUB flag to get rid of them
+ **Notice:** BTT TFT V3.0 will work in 12864 emulation mode but the encoder button does not. I assume it's a firmware bug since an original Ender-3 display works flawless (using -D USE_CREALITY_DISPLAY flag at compilation). This may not be the case if you've already updates your TFT firmware.

**2.13** - bug fixing

+ removed  the "playing tunes in background" feature since it was causing hangs and resets.
+ added parameter help on most of the GCodes when appending a question mark (?) to the command (i.e. M280?)

**2.12** - mostly code refactoring and a couple of new features

+ overhauled the intro in this README
+ added the [SKR mini E3 **V2.0**](https://www.biqu.equipment/products/bigtreetech-skr-mini-e3-v2-0-32-bit-control-board-integrated-tmc2209-uart-for-ender-4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) controller board to the build environments. Keep in mind that this controller board uses one hardware serial (Serial4) for communication with the TMC2209 stepper drivers and thus, the drivers are enumerated through the MS1/MS2 pins. Hence, you must setup the *DriverAddress* in the TMC configuration accordingly.
+ added support for the [LeoNerd OLED Module](https://www.tindie.com/products/leonerd/oled-front-panel-module/) as a replacement for my DIY display/encoder board.
This PCB is an out-of-the-box solution and is controlled completely through the TWI/I2C interface. Hence, it'll need only 4 wires to connect with (5 if RESET gets wired up too).
The slightly bigger OLED display (1.3") is also an improvement in terms of readability.
To activate it, set the **USE_LEONERD_DISPLAY** definition instead of **USE_xxx_DISPLAY** in platformio.ini.
*If you order one at the tindie store, make sure you to refer to the SMuFF project since you'll need a slightly modified firmware on the module.*
+ moved Materials from **SMUFF.CFG** into **MATERIALS.CFG** due to low memory issues when reading/writing the configuration file.
+ moved TMC settings from **SMUFF.CFG** into **TMCDRVR.CFG** due to low memory issues when reading/writing the configuration file.
+ added the F"*filename*" parameter to **M300**, which enables you to play a tune directly from SD-Card via GCode command.
+ added cursor keys evaluation (*Up*, *Down*, *Left*, *Right*) to the serial interface for controlling the menus via terminal (mainly for testing). *Up* and *Down* emulate the encoder wheel, *Right* the encoder wheel button and *Left* emulates clicking the "**Back**" option.
+ moved U8G2 library wrappers into a separate file (see U8G2Wrappers.cpp).
+ changed the behaviour in the menus UI so that separators will be skipped automatically.
+ moved list of available commands into files (mcmds.txt and gcmds.txt) to save memory. Therefore, you have to copy the **help** folder to your SD-Card.
+ moved menus and menu options into files located in the **menus** and **options** folders. Therefore, you have to copy those folders to your SD-Card.
+ moved the tune files into the **sounds** folder. Copy this folder to your SD-Card as well.
+ added I2C devices scanner at startup. If you compile for debug, you'll get a list of recognized I2C devices. Known devices will be shown by their names.
+ added support for the Adafruit Multiservo controller for up to 16 servos. Might come in handy in future versions (V5.x). To use this feature, you have to compile with the **-D MULTISERVO** option defined. **Please notice**: In version 2.4.0, this library will compile with error when using on the STM32 framework. You have to change the code manually and remove the 3rd parameter in call of *requestFrom* in the line that the compiler complains about.
+ refactored the source code quite heavily in order to keep the memory footprint (RAM) as low as possible.
**Please notice**: If you're about to add your own extensions in the firmware, try keeping the RAM usage **well below 90%**. Otherwise you may experience random hangs/resets because heap memory will colide with stack memory!
+ added *LBtnDown*, *LBtnHold*, *RBtnDown*, *RBtnHold* settings in SMUFF.CFG for **LeoNerd's OLED module**. Theses will take any GCode, which will be processed as the event occurs. This will enable you to configure the two soft buttons as you need them (i.e. Motors Off - M18 or Reset M999). The *RBtnHold* is predefined to open/close the lid servo if no other GCode has been applied to.
+ renamed **servoRevolver** to **servoLid** for better understanding.
+ renamed **Acceleration** to **AccelSpeed** in **SMUFF.CFG**.
+ added **MS3** to stepper sections of **SMUFF.CFG**. This setting is needed on the SKR E3-DIP, since the MS3 signal (used to setup the micro stepping) is connected to the MCU and thus needs to be set via software in case you have to. The setting can be either **0** (don't care), **1** (for setting it to LOW) or **2** (for setting it to HIGH).
+ refactored *smuffConfig* structure in SMuFF.h.
+ added individual servo closed position to each tool. This makes it easier to apply the right amount of pressure to each lid, especially when using the new levered lid closing mechanism. Changing the closed position from within the menu will take the currently selected tool into account.
+ replaced *NULL* with *nullptr* to avoid any compiler ambiguity in future releases.
+ added stall detection logic to the feeder as well. If you're going to use this feature, be aware that it'll slow down the feed speed to about a third of the normal speed. Though, it'll reduce feed errors and thus make the SMuFF more reliable. Read all about the setup [here](https://sites.google.com/view/the-smuff/how-to/tutorials/set-up-the-tmc2209?authuser=0).

**2.11** - More streamlining / bug fixing

+ **changed the speed settings** in configuration file, menus and GCode interface to **mm/s**. The timer tick value was kind of confusing and misleading.
+ dumped **MaxSpeedHS** parameter since it's not really needed and confuses people.
+ fixed a couple of bugs induced in 2.10.
+ optimized code for TMC2209 stepper driver and stall detection/handling.
+ all sounds can now be modified and are contained in the **.DAT* files of the **Tunes** folder.
+ added new parameters to [M205 GCode](https://sites.google.com/view/the-smuff/tips-hints/talk-to-the-smuff?authuser=0#h.g5l7kws0923c) command.

**2.10** - A lot of changes, such as TMC driver support; **Please read on**

+ finished the implementation of the Duet3D Laser Sensor (V2) which can be used as the Feeder endstop and is able to monitor filament jams.
+ added GCode **M412** which will switch on/off runout/jam detection or report its status, when using a Duet3D Laser Sensor.
+ removed configuration file variants. There's only one general config file left.
+ renamed configuration file from **.CFG** to **.CFG.json**. This makes it easier for some after market *VS-Code extensions* to validate and format its content. **Please notice:** This file is meant as a template for your initial configuration. Make sure you rename the template file to "**SMuFF.CFG**" after you've copied it onto the SMuFF's SD-Card.
+ added GCode **M17** which enables you to switch a relay in order to switch from external stepper (3D-Printer) to internal stepper (SMuFF). The parameter must either be **E** for the **external** or **I** for the **internal** stepper. The relay is controlled over the **RELAY_PIN** in Pins.h. Read more about this [new feature here](https://sites.google.com/view/the-smuff/work-in-progress?authuser=0#h.qbpb6pvlq20x).
+ overhauled Settings Menu (moved additional settings into Options menu).
+ added **Serial0Baudrate** (for USB port) to config files, renamed **SerialDueBaudrate** to **Serial3Baudrate**.
+ fixed a bug for the old Revolver version where it refused to home correctly.
+ added defines for SERVO_LID and SERVO_WIPER for better code readability.
+ changed the behavior of boolean inputs (YES/NO and HI/LO) in the menus (they're single click now).
+ changed the increments on all stepper speeds (they'll now increment/decrement by 5).
+ moved some of the most common build flags (i.e. USE_xxx_DISPLAY) to the top of [platformio.ini](https://sites.google.com/view/the-smuff/how-to/tutorials/compile-the-firmware?authuser=0#h.3e6724efr6vl).
+ moved all initializing functions into **SetupInit.cpp**. SMuFF.cpp and setup() got much more streamlined now.
+ moved all periodical functions into **Periodicals.cpp**.
+ periodicals are now called from within **loop()**, which makes them more stable when handling serial I/O.
+ added the [SKR mini E3 V1.2](https://www.biqu.equipment/products/bigtreetech-skr-mini-e3-control-board-32-bit-integrated-tmc2209-uart-for-ender-4) and [SKR mini E3 DIP V1.1](https://www.biqu.equipment/products/bigtreetech-skr-e3-dip-v1-0-motherboard-for-ender-3) to the collection of usable boards.
+ rewrote the timers code. Encoder, Servos and Fans are now being served by one general purpose timer only. Servos are far less jittery now.
+ added *TMC-Stepper library* for being able to support TMC2209 stepper drivers.
+ added TMC-Params to the stepper menus. You'll need those settings at least on the SKR mini **E3**, on the SKR mini **E3DIP** when using TMC2209s.
+ added GCodes **M122**, **M350**, **M569**, **M906** and **M914** for handling TMC stepper driver settings (see Marlin GCode what they're used for).
+ got the USB port working on E3 and E3 DIP on Windows.
+ added a couple of more parameters supported by the [M205 GCode](https://sites.google.com/view/the-smuff/tips-hints/talk-to-the-smuff?authuser=0#h.g5l7kws0923c) command.

**2.09** - Bugfix for PMMU mode

+ fixed the bug which didn't realize the **A**(bort) command comming from Marlins MMU code
+ added **SOFTRESET** option for Marlin in MMU2 mode. This will not initiate a hard reset on the SMuFF, instead it'll pretend to have been reset. This option was needed because some bootloaders will send various information over the serial interface at boot and thus confuse the MMU2 code in Marlin.
+ added build flag **MARLIN2_ONLY** to overcome incompatibilities between Marlin 2.0 and Prusa firmware. Remove this build flag **only** when you're intending to run the SMuFF on a Prusa MK2/3/S.

**2.08** - Added Display menu in settings

+ new menu "Display" in settings lets you define stuff as Power save timeout, LCD Contrast and Backlight color
+ Backlight color of either RGB or NeoPixel displays will be saved to the SMuFF.CFG
+ added **M150** to set LED color (RGB or NeoPixel) via GCode. Parameters are same as on Marlin. Parameter **C*x*** allows you to set all LEDs to one of the predefined color indices (Black, Red, Green, Blue, Cyan, Magenta, Yellow, White) starting with 0 for Black (i.e. *M150 C4* sets all LEDs to Cyan). Parameter **S*n*** lets you define the LED index on NeoPixel LED stripes (starting at index 0 for first LED).

**2.07** - Added FastLED to project

Since some displays nowadays come with a NeoPixel backlight, I've seen the urge to add the FastLED library, which controls NeoPixels in a very comfortable way.
Though, on the STM32 Maple framework it will not compile right away, but there's a workaround. Please read the comments above the initFastLed() function carefully.

**2.06** - Changes for USB connection

+ made the USB serial port available for controlling the SMuFF. Comes in handy when operating on OctoPrint (Raspberry Pi), might not work on Windows though.
+ added some more //action: commands for OctoPrint plugin

**2.05** - Optimization for external control (i.e. OctoPrint plugin)

+ added WipeSequence setting to *SMuFF.CFG*.
This setting defines how the wiper servo will run. The sequence is a string in the format "**S**nn **I**nn **J**nn **P**nn **R**nn". Where **S** defines the speed (wait in millis between each movement), **I** defines the angle of the first position while wiping, **J** the angle of the second position, **P** the angle of the released position and **R** the number of repeats between **I** and **J**. This sequence will be overridden if passed as paramters of the **G12** GCode command.
+ changed "Servo cycles" to "Servo 2 cycles" and added "Servo 1 cycles", so each servo has it's individual settings

**2.04** - Optimization for OctoPrint plugin

+ added option to continously send status informations (current tool, endstop states) every two seconds
+ added option to engage/disengage 2nd servo via GCode (M280 P1 R0/1)
+ added filter for printable characters only while receiving data
+ added wrap for u8x8_byte_arduino_2nd_hw_spi in order to use SPI3 for the RepRap display on the SKR Mini V1.1
+ added wrap for u8g2_UserInterfaceMessage in order to be able still receiving commands from the serial interfaces

**2.03** - Minor changes

+ maxed out the number of  tools to 15.
+ added option to build firmware to be flashed from the SD-Card for the SKR mini V1.1 in order to prevent the stock bootloader from being overwritten.
+ fixed bug on ESP32 build in ZServo.cpp.

**2.02** - Added more support for SMuFF V5

+ changed some strings in the settings for V5.
+ removed Revolver settings if compiled for SMuFF_V5.
+ added Servo open/close in main menu.
+ added Tool Maintanance in main menu - this one moves the selector carrier two tools either left or right, so you can easily access the current tool if needed.
+ added Servo min. and max. PWM settings in the CFG file. These are representing the PWM signal length in microseconds. Usually set to 1000 (1ms) for 0 deg and 2000 (2ms) for 180 deg.
+ added Servo_Test.gcode to the test folder. Run this to test the positioning of your Revolver-Servo. Make sure the servo is able to reach all positions between 0 and 180 deg before you execute this test run.
+ added GCode command **TM** to the GCode-Parser whitch toggles the Tool Maintanance mode.
+ reworked the ZServo library for STM32 to get a stable and clean 50 kHz signal for driving the servos. Please notice that some micro servos are not very good in handling 3.3V PWM signals. Hence, the servo pins on the SKR mini have moved to the control signals of the Y-Stepper driver (if compiled for SMuFF_V5), which allow 5V tolerance and Open-Drain mode. This comes in handy, as the output PWM signals then can be pulled up to 5V.

**2.01** - Added support for a custom ESP32 controller board.

+ Please notice that this board doesn't exist yet. If you're keen to build one, you'll find the circuit diagramm in the Schematics folder. The base for this controller board is a ESP32 "NodeMCU devkit1" which is easy to get.
+ cleaned up platformio.ini. Be aware that from V2.xx on 8 bit controllers (such as the ATMega2560) will not be supported for this project anymore and the firmware code might not compile correctly.
+ tested configurations for other boards like the SKR 1.3/1.4. Theses boards can't yet be used as controller boards for the SMuFF because the framework for LPC176x MCUs do not support the Arduino standard and compiling will fail without adding some sort of HAL to it. Though, as the development of these platforms improve rapidly, this might not be an issue in the future anymore.

---

**1.67** - Bugfix for SKR in Duet3D mode

+ fixed sending endstop states to wrong serial port for Duet3D. Please notice: In Duet3D mode you **must use** the Serial 1 (the one labeled TFT on the board). Serial 3 will not receive the endstop states, which are needed to make the scripts on the Duet3D work correctly.

**1.66** - Buxfix for Wanhao i3 mini

+ fixed compile time error in ZServo for Wanhao i3
+ fixed compile time warnings for Wanhao i3

**1.65** - Minor changes - mainly for servo variant

+ changed the servo timing (duty cycle was twice as long as it's supposed to).
+ added live position change while configuring the servo positions in the menu (opened/closed).
+ added option to set up the servo pulse cycles (0 means: cycle forever, any value above 0: cycle only *n* times). *Set this value to about 2-3 if you experiencing jitter on the servo.*
+ added "**UseServo**", "**ServoOpened**" and "**ServoClosed**" parameters to M205 GCode command.

**1.64** - Minor changes

+ reworked the acceleration/deceleration algorithm for the stepper motors.
+ changed some default speed settings in the SMuFF.cfg file for SKR (due to the reworked acceleration/deceleration).
+ modified some of the test scripts for automated testing.
+ added M98 GCode to enable startig test runs from GCode (M98 P"filename" - omit the file extension ".gcode"). *Please notice: Since serial communication is disabled during test runs, you'll have to stop them by pressing the encoder button.*
+ reworked timer usage on STM32.
+ reworked servo library.

**1.63** - Minor changes

+ Wiggling the Revolver is now an option in the settings.
+ Added Feed error count to test run info display.
+ Added ok/missed feeds to test run. You'll need a 2nd endstop at the end of the bowden tube, which gets connected to the X+ endstop port on the SKR mini.
+ On feed errors, firmware will now retry 4 times before giving up. On second retry it'll home and reset the Selector. On third retry it'll go through all tools and retract the filament a bit (to prevent other tools/filaments blocking the Selector), then reposition the Selector as well.
+ Modified the servo module, so that it can handle more than one servo. Also, redefined the pins for the servo in the Pins.h. Servos are now driven by the endstops Y+ and Z+ ports.
+ Added experimental code to replace the Revolver stepper motor with a standard sized servo. This is still work in progress.

**1.60** - New enhancements

+ restructured the Main Menu.
+ added **Settings Menu** - *now, almost all parameters can be changed comfortably through the UI and saved to the SD-Card.*.
+ added long click to main screen for a quick access of the *Settings Menu*.
+ added long click in each setting dialog to close the dialog and discard the changes made.
+ added M500 (save to EEPROM) and M503 (read EEPROM) GCodes. Latter will give you a JSON format output, like the contents of the SMUFF.CFG file.
+ dropped the **Materials** section from within the configuration file due to memory limitations on the ATMega (make sure you remove it completely from your config file, otherwise your controller might hang on startup).
+ added **Reset Feeder Jam** to the *Main Menu*, dropped the double click action for this from last version.
+ did some code clean up, extracted menu- and dialog functions into separate files.
+ moved the ClickEncoder library source into the project since I needed some code enhancements (resetButton).
+ added **Testrun Menu** - an integrated test function (SKR only) - *place scripts with GCodes on the SD-Card which will get executed one by one in a continous loop*.
+ added some test scripts to the **test** folder - *copy those onto your SD-Card o  use them* .

**Please notice:**
This version will be the last one compatible with the **Wanhao i3 mini** (or 8-Bit in general)!
With the development going on, the memory limitations on 8-Bit devices are a real deal breaker.
For example: The only way to reach the *Settings Menu* screen is the long click on the main screen. The way it works on the SKR mini (through the *Main Menu*) crashes on the ATMega because of low working memory. For the same reason I've got to leave out the testrun option.

Hence, I've decided to focus on the 32-Bit devices in future versions.
If you've already assembled your SMuFF with the Wanhao i3 mini controller, it's fine. There's no need to switch over to the SKR mini unless you *really badly need* some of the enhancements and extensions that may come in the future.

**1.56** - Optimization

+ added resetting the "Feder Jammed" state by double clicking the encoder button.
+ removed the ZPwm.cpp / ZPwm.h since it's not needed.

**1.55** - Optimization

+ reworked Revolver movement - much smoother now.
+ optimized stepper motor speeds for SKR in configuration file.
+ Tools swapping is now being stored in the EEPROM.DAT file so that swaps will survive a reset.
+ added Cancel / Retry option when loading fails.
+ sound (beeper) now works flawlessly on SKR (STM32).
+ SKR still has issues with the fan (it's either full speed or no speed).

**1.53** - This version has got some major changes:

+ Full integration of the SKR mini V1.1 controller board (STM32) completed.
+ Prusa MMU2 Emulation mode improved even more.
+ Heavy refactoring to make the code better readable.
+ Optimized memory usage (all strings are now located in PROGMEM).
+ replaced the Rotary Encoder library.
+ Header files are now located in the include folder.
+ Pins header file separated into subfolders for different devices (uses the  -I compiler directive).
+ Added Configs folder containing different configuration samples for the modes/controllers.
+ Platformio.ini modified to allow different build environments.
+ Moved datastore from EEPROM to SD-Card (mainly because of the STM32).
+ Indexer for Materials in SMUFF.CFG renamed from Tool0..x to T0..x (because of memory issues).
+ Added *FeedChunks* and *EnableChunks* settings to SMUFF.CFG. Those are needed since the communcation on the 2nd serial port tends to hand in long operations (such as feeding the filament to nozzle) and Prusa won't be able to abort the feed.
+ Added *StepDelay* setting to SMUFF.CFG for the SKR Mini. This is needed because of the speed of a 32 bit board to keep the steppers from stalling.
+ Added schematics of the SKR Mini LCD board.

**1.4**  - Major changes to gain better compatibility for Prusa Emulation Mode and setup for a different platform (STM32). Latter is unfinished yet.
The configuration file (SMUFF.CFG) has got a new setting which defines the distance from the filament guide to the Selector (see *SelectorDist* setting).

**1.3**  - Some modifications to gain Prusa MMU2 compatibility

**1.2**  - Initialy published version

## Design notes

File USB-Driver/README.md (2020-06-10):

# USB-Driver(s)

This folder contains a .INF file for the SKR mini V1.1, which is needed to install a driver on Windows in order to access the USB serial port.

**Notice:** As of now, this file might not be suitable for your Windows version.

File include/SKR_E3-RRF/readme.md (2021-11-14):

** Do not use **

This board configuration is used for testing and it's not officially supported yet!

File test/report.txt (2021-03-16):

{ESC:01;01f}GCode: {ESC:30m}{ESC:42m}{GCO}{ESC:40m}{ESC:37m}
{ESC:03;01f}Elapsed:      {ESC:35m}{TIME}{ESC:37m}
{ESC:03;28f}Loops:         {ESC:35m}{LOOP}{ESC:37m}
{ESC:03;50f}Cmds:             {ESC:35m}{CMDS}{ESC:37m}
{ESC:04;01f}Tool Changes:      {ESC:36m}{TC}{ESC:37m}
{ESC:04;28f}Feeder Errors: {ESC:31m}{ERR}{ESC:37m}
{ESC:04;50f}Stalls (S/F) :{ESC:31m}{STALL}{ESC:37m}/{ESC:31m}{STALLF}{ESC:37m}
{ESC:06;01f}                 T0  |   T1  |   T2  |   T3  |   T4  |   T5  |   T6  |   T7  |   T8  |   T9  |  T10  |  T11
{ESC:07;01f}Feeds ok     : {ESC:35m}{HIT}{ESC:37m}
{ESC:08;01f}Feeds missed : {ESC:31m}{MISS}{ESC:37m}

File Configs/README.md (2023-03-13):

# Configuration Files

Copy these files onto the SMuFFs SD-Card **root folder** (/) before you flash the firmware.

*Please keep in mind that these files are not needed for flashing the firmware but for the runtime of the SMuFF! Hence, this SD-Card has to remain in its slot all the time.*

The filenames are supposed to be self explanatory.

**Please notice:** *You don't have to modify the contents of the JSON files manually, since they're covered by the menus and GCode interface.
Although, you can if you feel the urge to do so. Just use a JSON capable editor (i.e. VSCode) to ensure the format doesn't get messed up, which will eventually render the files useless.*

---

The **debug.txt** file contains the debug output flags, which is being read before the SMuFF starts up in order not to miss any information.
*If you want to change the default debug output behaviour of the firmware, simply edit this file in a text editor.*

The (binary encoded) value of *15* is the default setting, whereas *255* means "show all". For a more specific defintion see *debug.h*:

```C++
#define D       1
#define W       2
#define I       4
...
```

If the value is followed by a semicolon ( **;** ) and a number between **0** and **3**, the firmware will route debug messages to the according serial port:

+ 0 = USB
+ 1 = Serial1
+ 2 = Serial2
+ 3 = Serial3

*Serial2* is by definition the default port for debug messages, which usualy is located at the **TFT** header.
*Please keep in mind: Not every serial port is available on all of the supported boards. The file "Pins.h" contains a couple of CAN_USE_SERIALx definitions that tells which serial port is available in general.*

If you set the debug port to **USB (0)**, make sure you **undo** this change before you attach the SMuFF to **OctoPrint** for example, because otherwise this will mess up the communication with the [OctoPrint SMuFF plugin](https://github.com/technik-gegg/OctoPrint-Smuff), which usually runs via the USB.

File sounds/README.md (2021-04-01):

# Tunes

This folder contains tunes (sounds), which are used by the SMuFF firmware.
Copy those tunes into the SD-Cards *sounds* folder in order to be able to modify those sounds.

The content of such tune file looks like this:

```text

F440 D120 P150. F523 D120 P80. F196 D220 P80. F196 D120 P80. F587 D400 P120.F349 D80 P240.
```

It's a plain text file which consists of a list of tones (up to 150 characters), represented by **F** as the tone frequency (in Hz), **D** as the tone duration (in mS), **P** as the pause (in mS) after the tone has played and the period ( **.** ) as a delimiter between tones.
The **P**(ause) parameter can be left out but the period ( . ) is **mandantory** for the tone to be played!
Spaces in between can be placed for better readability and may be omitted.

If you'd like to compose your own melodie/sound, use the **M300** GCode command to test it out.

The naming scheme used for these files is hard coded in the firmware (extension has to be *.DAT*):

+ STARTUP - is the startup melody
+ BEEP - is the default single beep tone
+ LBEEP - is a longer beep tone, used to signal errors
+ UBEEP - is a short sequence signaling user attention is required
+ EBEEP - is the encoder tick tone

**STARTUP_NEW** and **STARTUP_SW** are variations of the startup tune - later is for StarWars fans only! (copy over to STARTUP.DAT to use one of these instead).

**EBEEP_LEONERD** is a modified encoder tick tone for LeoNerd's OLED Module (copy over to EBEEP.DAT to use this one instead).

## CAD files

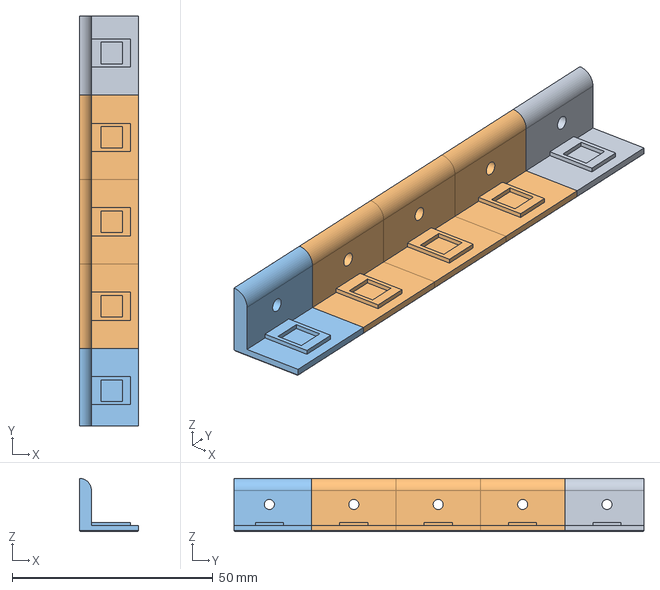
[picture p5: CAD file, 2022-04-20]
STEP/V6/LED-Diffusor.stp
14.8 x 102.0 x 13.3 mm

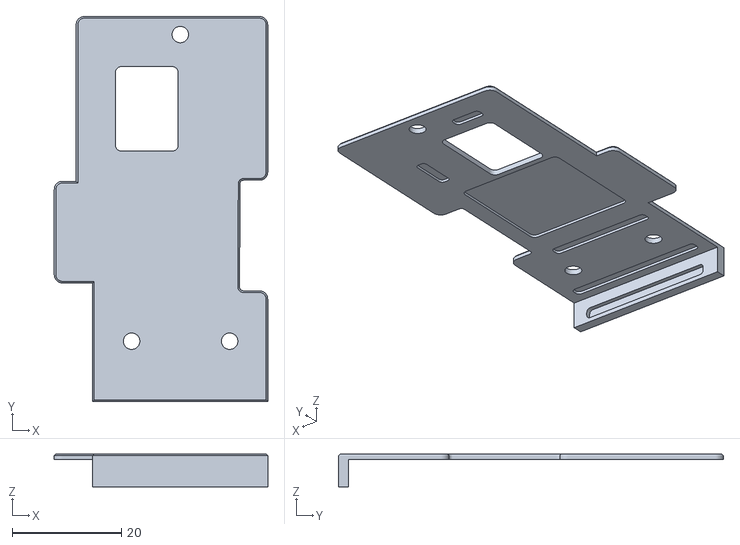
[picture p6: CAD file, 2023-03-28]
STL/V6/Base/Connector-PCB-Top-Cover.stl
39.0 x 70.3 x 6.00

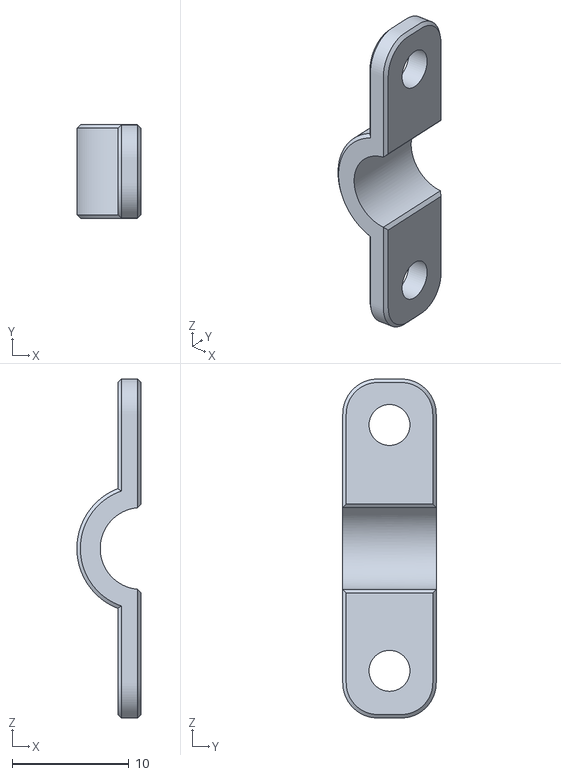
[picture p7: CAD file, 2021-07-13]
STL/V6/Cable-Clamps/Cable-Clamp-Big.stl
5.50 x 8.00 x 29.0

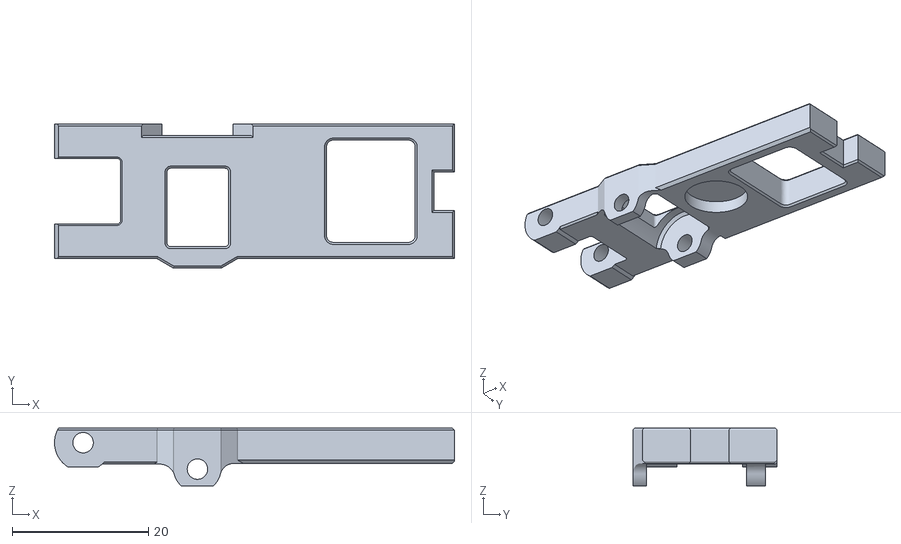
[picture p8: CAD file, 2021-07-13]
STL/V6/Filament-Guides/Filament-Guide-Lid-Magnet.stl
58.7 x 21.2 x 8.50

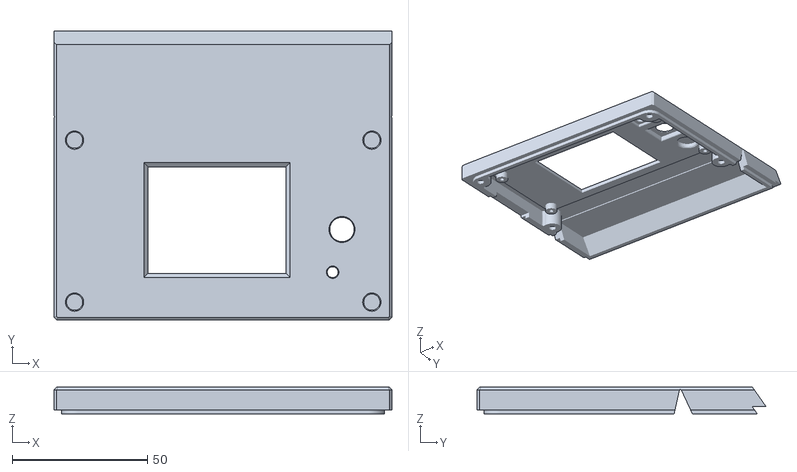
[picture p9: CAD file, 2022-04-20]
STL/V6/Housing/Housing SKR New-Lid-BTT24.stl
125.0 x 106.9 x 9.90

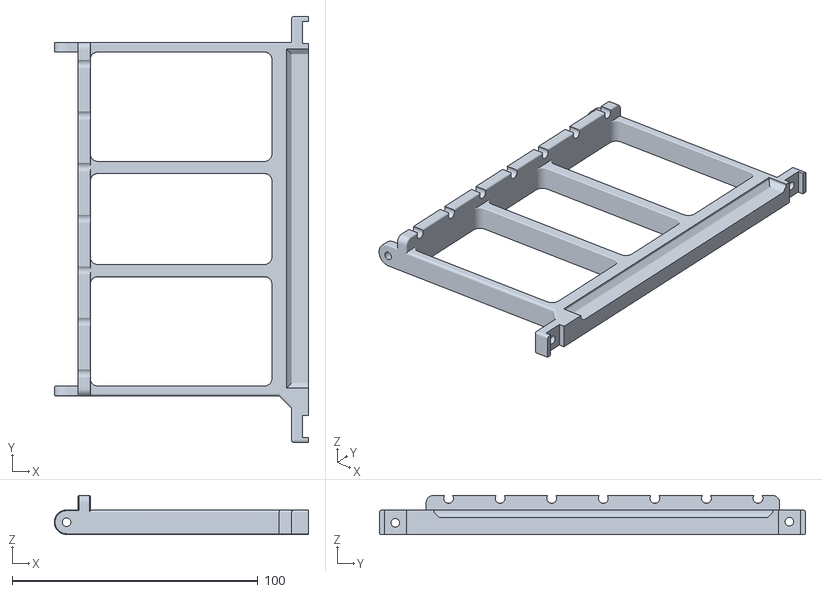
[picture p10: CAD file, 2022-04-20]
STL/V6/Inlet-Guide/Inlet-Guide-1 (7 tools).stl
103.6 x 173.5 x 16.0

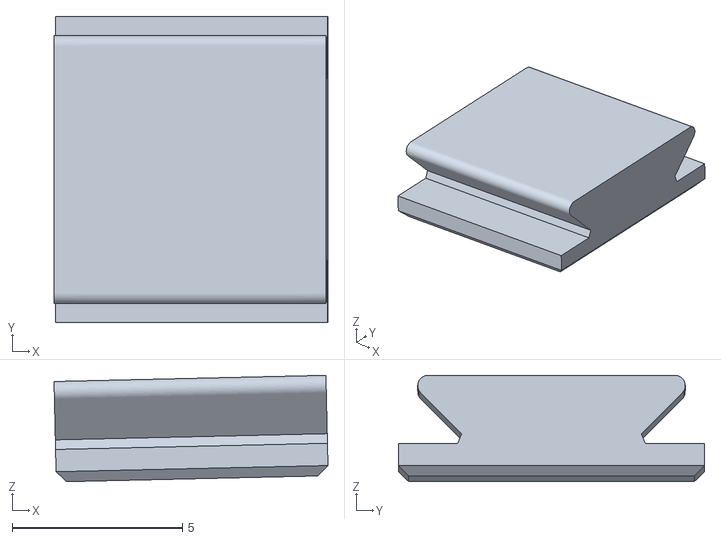
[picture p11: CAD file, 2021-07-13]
STL/V6/Lever/Lever-Distancer-Small.stl
8.06 x 9.00 x 3.13

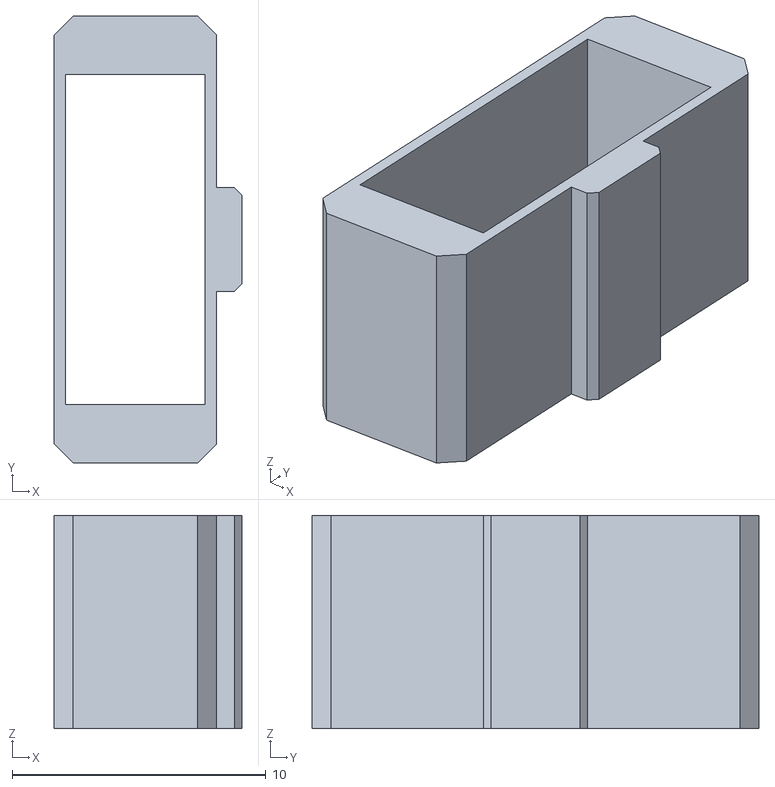
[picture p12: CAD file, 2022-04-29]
STL/V6/Other/Dupont-5x2-key.stl
7.40 x 17.6 x 8.40

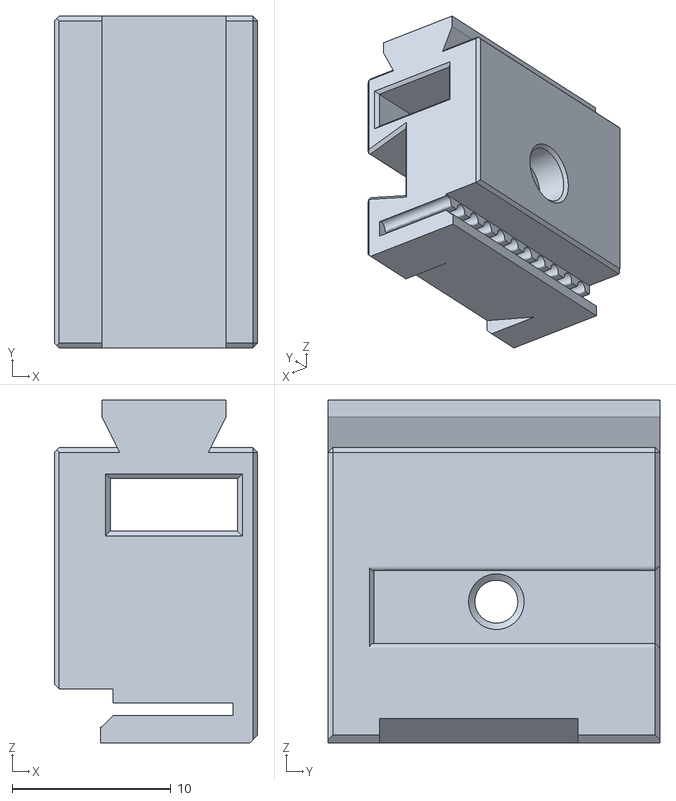
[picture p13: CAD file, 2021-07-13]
STL/V6/Selector/Selector-Carrier-Belt-Clamp.stl
12.8 x 20.9 x 21.6

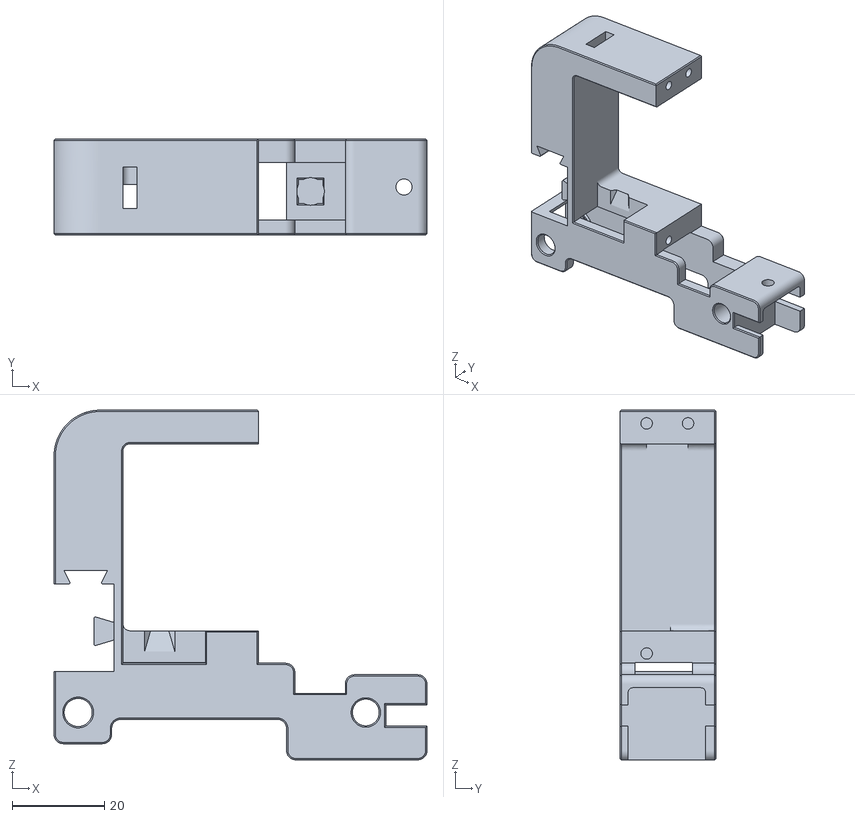
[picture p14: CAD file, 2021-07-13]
STL/V6/Servo-Mount/Servo-Carrier.stl
81.1 x 20.9 x 76.0

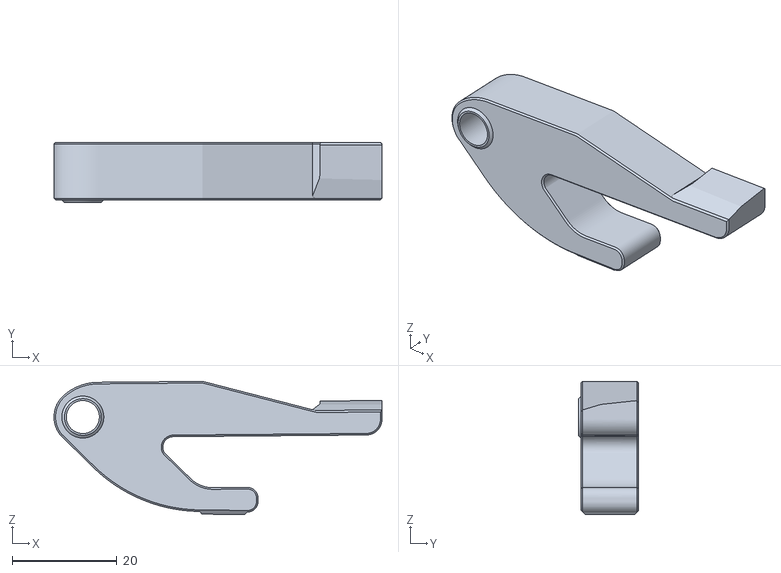
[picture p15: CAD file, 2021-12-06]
STL/V6/Small Servo-Carrier/Servo-Small-Lever.stl
62.5 x 11.5 x 25.4

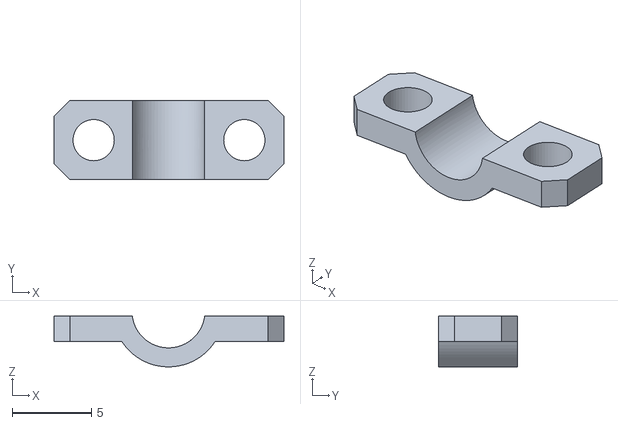
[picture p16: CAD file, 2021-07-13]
STL/V6/Splitter/Splitter-Cable-Clip.stl
14.5 x 4.98 x 3.20

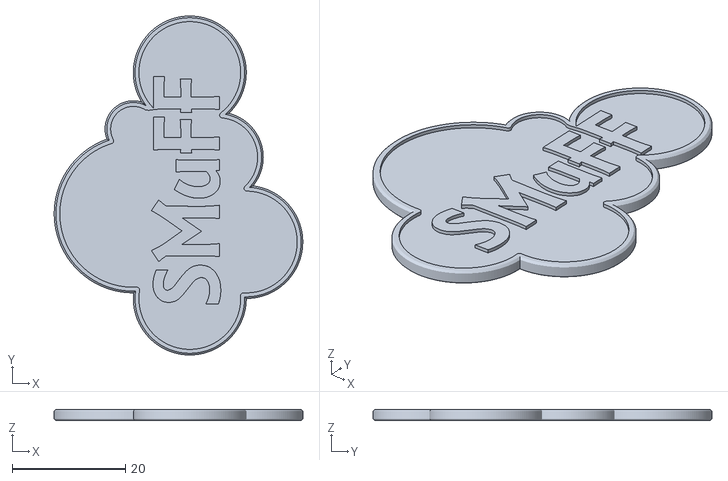
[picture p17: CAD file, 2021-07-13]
STL/V6/Test-Model/Test-Print-Bottom.stl
44.0 x 60.0 x 2.00

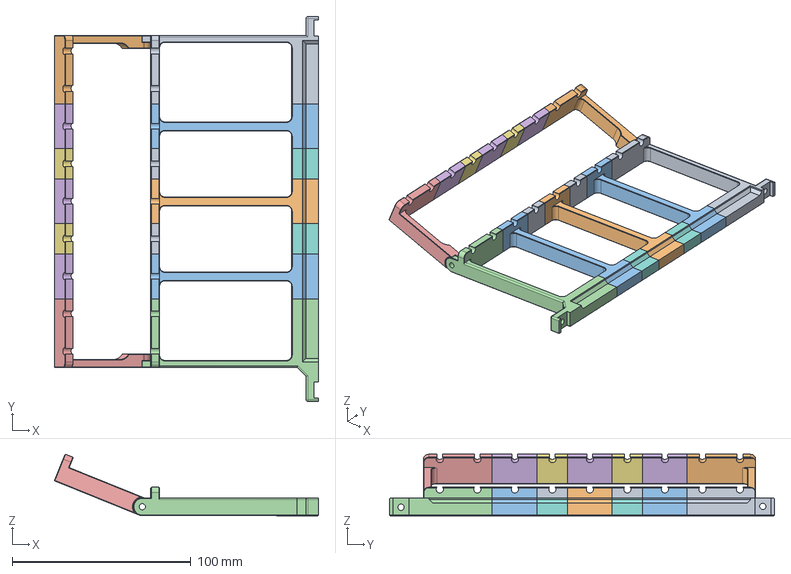
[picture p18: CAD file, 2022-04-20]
STEP/V6/Inlet-Guides.stp
147.8 x 215.5 x 34.4 mm

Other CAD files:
STL/V6/Base/Connector-PCB-Mount.stl
STL/V6/Cable-Clamps/Cable-Clamp-Bottom.stl
STL/V6/Filament-Guides/LED-Diffusor.stl
STL/V6/Housing/Housing SKR New-GoPro-Mount.stl
STL/V6/Base/Base-Left-Cable-Cover.stl
STL/V6/Base/Base-Left-Gear-Cover.stl
STL/V6/Base/Base-Left-Strain-Relief.stl
STL/V6/Cable-Clamps/Cable-Clamp-Small.stl
STL/V6/Filament-Guides/Filament-Guide-Front-Splitter.stl
STL/V6/Filament-Guides/Filament-Guide-Front.stl
STL/V6/Filament-Guides/Filament-Guide-Lid.stl
STL/V6/Housing/Housing SKR New-Lid-DIY.stl
STL/V6/Housing/Housing SKR New-Lid-FYSETC24.stl
STL/V6/Housing/Housing SKR New-Lid-LeoNerd.stl
STL/V6/Housing/Housing SKR New-Top-Lid.stl
STL/V6/Housing/Housing-Lid-BTT24.stl
STL/V6/Housing/Housing-Lid-BTT35.stl
STL/V6/Housing/Housing-Lid-FYSETC24.stl
STL/V6/Housing/Housing-Lid-Spacer-5mm.stl
STL/V6/Housing/JST-Holder.stl
STL/V6/Housing/Sy8205-Spacer.stl
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

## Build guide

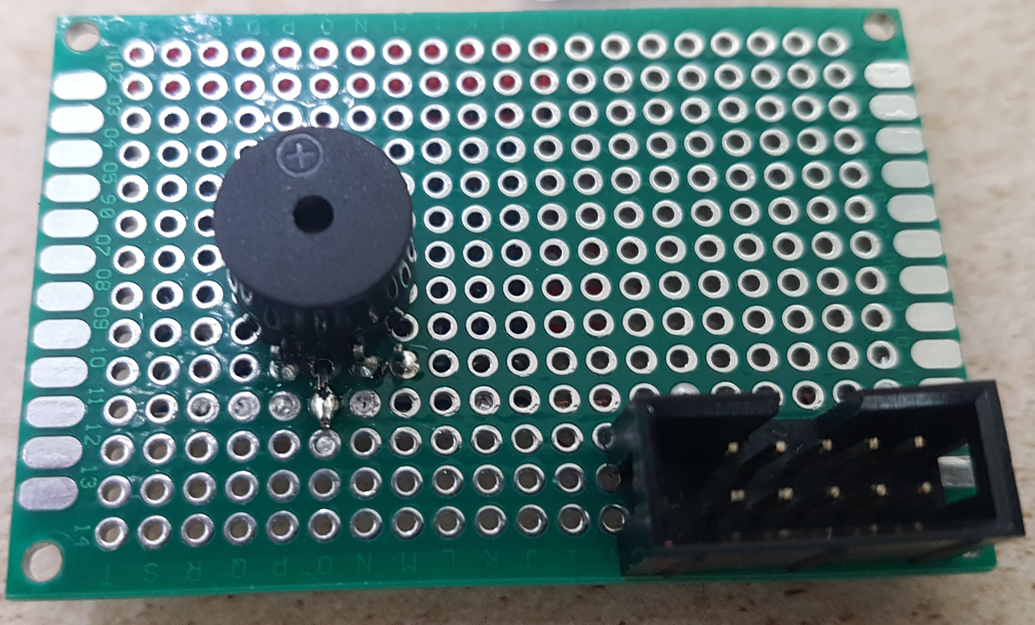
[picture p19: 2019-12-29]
images/SKR Display/Step_4a.jpg

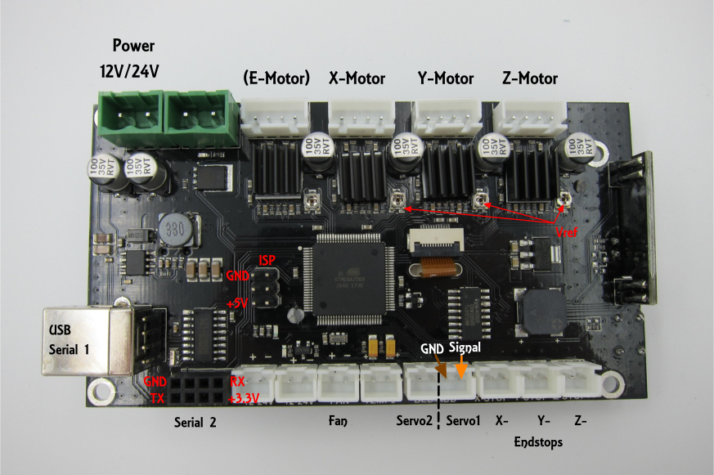
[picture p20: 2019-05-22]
images/Wiring.png

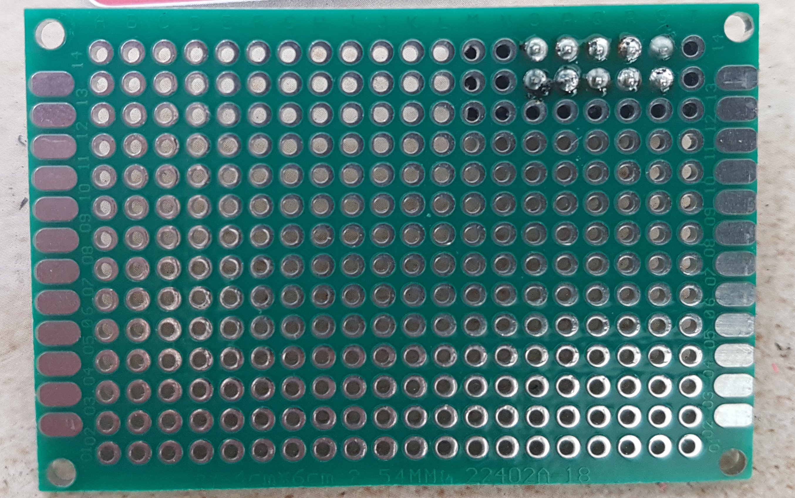
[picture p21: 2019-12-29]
images/SKR Display/Step_1a.jpg

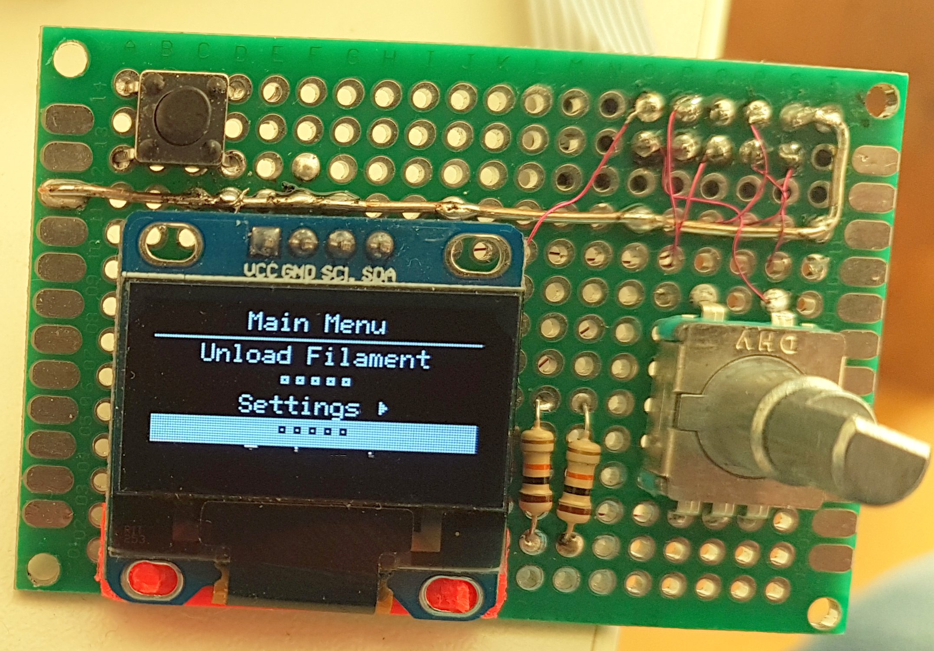
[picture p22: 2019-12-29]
images/SKR Display/Step_10.jpg

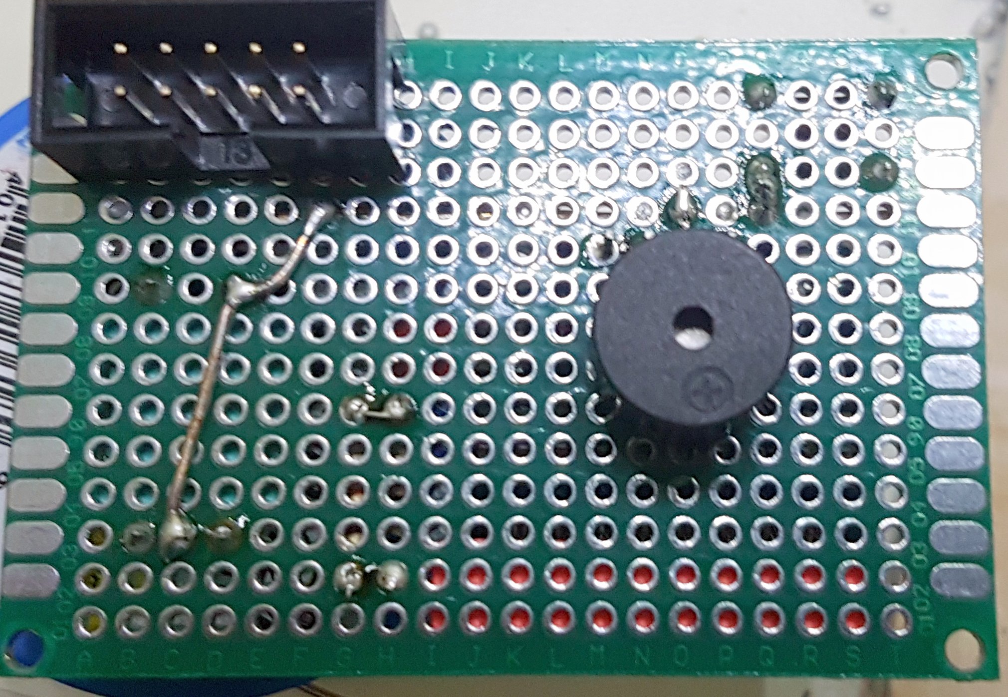
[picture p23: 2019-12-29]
images/SKR Display/Step_6.jpg

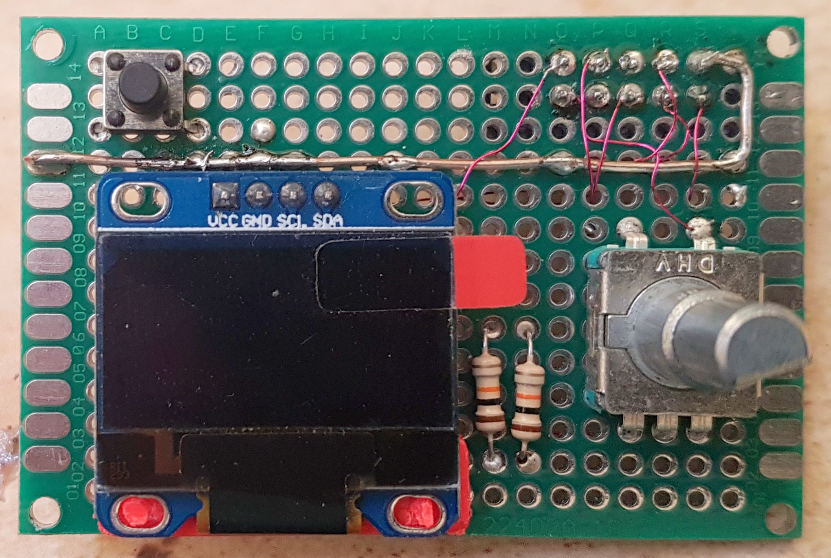
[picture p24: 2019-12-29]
images/SKR Display/Step_8.jpg

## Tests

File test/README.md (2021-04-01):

# SMuFF Test GCode Scripts

These test scripts may be used for initial testing of the SMuFF after you built it, to ensure the build has no mechanical or electrical issues.
To use these scripts, simply copy them to the root folder of your SD-Card for the SMuFF.
In the Main Menu on the SMuFF, you'll find a menu item called **Testrun**. Select this and you'll get a list of the script files located in the test folder of your SD-Card.
Pick one to start the test.

Feel free to modify the test scripts to adopt them to your needs. Test scripts are GCode scripts, which will get parsed and interpreted by the SMuFF at runtime.
Each GCode command has to be put in a separate line. Comments start with a semicolon ( ; ) and will be ignored by the interpreter.

For randomizing tools, you may place a *{RNDT}* macro somewhere in the GCode (i.e. **T{RNDT}**). The test run function will then generate a random number between 0 and the number of tools defined in the configuration file, trying to avoid using the same tool twice.

The **report.txt** file contains the text which will be sent to the log serial (usually USB-Serial), in order to display the results while the test is running.
This file is set up to display a formatted output on a **VT100** compatible terminal program. To achive this, it utilizes VT100 ESC sequences for coloring and cursor positioning. If needed, you can use any of the available VT100 ESC sequences. Look them up [here](http://ascii-table.com/ansi-escape-sequences-vt-100.php).
Feel free to modify the reports.txt file in order to get the output you want.

In this file you'll also find a couple of macros, defining which information to print where. Those macros will be replaced by the actual values at runtime:

- {TIME}    - prints the elapsed testing time
- {GCO}     - prints the current GCode executed
- {ERR}     - prints the error count (failed feeds)
- {LOOP}    - prints the loop count
- {CMDS}    - prints the overall commands processed count
- {TC}      - prints the tool changes count
- {STALL}   - prints the overall stall count (only with TMC2209 drivers)
- {HIT}     - prints the hit count of feeder endstop 2
- {MISS}    - prints the missed count of feeder endstop 2

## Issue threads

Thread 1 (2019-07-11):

Use SMuFF with Klipper Firmware

troisplus, 2019-07-11:
Hi,
I wanna know if you already thought about klipper compatibility. It combines the power of a raspberry Pi 3 with one or more micro-controllers.
(https://github.com/KevinOConnor/klipper)

Actually I use a Anet A8 running klipper with an arduino mega/ramps shield. I used marlin few month ago but had poor quality prints.
I hope to install a MMU system with multi controlers on RPi3

technik-gegg, 2019-10-13:
Hi troisplus,
sorry for the late reply. I wasn't ignoring your request, I simply got no notification about it.

No, I havent thought  about Klipper as of yet but that's not really necessary.
I wrote the code for the SMuFF in a way that will make it easy for any firmware to support the SMuFF as long as it can handle a serial port and can talk GCode (which eventually means: all of them ;o).

So, if a firmware wants to utilize the SMuFF, it simply sends the Tx command over the serial interface and the SMuFF will do the rest.

By looking at the code you sent me in the link, I can't see any support for tool changing. But as much (or little) as I know about Klipper, I think it's configurable somewhere.
Do you have any links of samples for other tool changing hardware supported by Klipper?
If so, please let me know and I'll take a look.

flopana77, 2020-10-15:
Hi technik-geeg
I am also looking at running the SMuFF via Klipper. That said, I wanted to build the V5 and didn't put my mail address in the donation...Is there any way we can get in contact regarding the stl-files and to discuss the Klipper implementation later on?
Cheers

technik-gegg, 2020-10-15:
I've already sent you an email with the files.

As far as it concerns Klipper, I haven't had the chance yet to set it all up (with the latest Klipper modifications). Though, there's at least one member on the Discord channel (Carpediem1903) who's after this as well.
You're invited to join and discuss along.

Closed 2019-12-14.

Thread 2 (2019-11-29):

error: 'uint32' does not name a type

paulpenney, 2019-11-29:
Hello!

Just getting this error when I am trying to compile for the Wanhao board. Tried on both VScode and Atom, but the same issue. Any ideas?

paulpenney, 2019-11-29:
Here is the terminal:

Processing WANHAO_I3_MINI (platform: atmelavr; framework: arduino; board: megaatmega2560)
--------------------------------------------------------------------------------------------------------------------------------------------------------------------------------------------------------------------------------------------------
Verbose mode can be enabled via `-v, --verbose` option
CONFIGURATION: https://docs.platformio.org/page/boards/atmelavr/megaatmega2560.html
PLATFORM: Atmel AVR 2.0.0 > Arduino Mega or Mega 2560 ATmega2560 (Mega 2560)
HARDWARE: ATMEGA2560 16MHz, 8KB RAM, 248KB Flash
PACKAGES: framework-arduino-avr 5.0.0, toolchain-atmelavr 1.50400.190710 (5.4.0)
LDF: Library Dependency Finder -> http://bit.ly/configure-pio-ldf
LDF Modes: Finder ~ chain, Compatibility ~ soft
Looking for U8G2 library in registry
Found: https://platformio.org/lib/show/942/U8g2
LibraryManager: Installing id=942
U8g2 @ 2.27.2 is already installed
Found 10 compatible libraries
Scanning dependencies...
Dependency Graph
|-- <SdFs> 2018.6.24
|   |-- <SPI> 1.0
|-- <ArduinoJson> 6.13.0
|-- <MemoryFree> #a2d60bd
|-- <Wire> 1.0
|-- <SPI> 1.0
|-- <U8g2> 2.27.2
|   |-- <Wire> 1.0
|   |-- <SPI> 1.0
Building in release mode
Compiling .pio\build\WANHAO_I3_MINI\src\ClickEncoder.cpp.o
In file included from src\ClickEncoder.cpp:12:0:
include/ClickEncoder.h: In constructor 'ClickEncoder::ClickEncoder(uint8_t, uint8_t, uint8_t, uint8_t, bool)':
include/ClickEncoder.h:116:29: warning: 'ClickEncoder::doubleClickEnabled' will be initialized after [-Wreorder]
   bool doubleClickEnabled = false;
                             ^
include/ClickEncoder.h:109:31: warning:   'bool ClickEncoder::accelerationEnabled' [-Wreorder]
   bool  accelerationEnabled = false;
                               ^
src\ClickEncoder.cpp:46:1: warning:   when initialized here [-Wreorder]
 ClickEncoder::ClickEncoder(uint8_t A, uint8_t B, uint8_t BTN, uint8_t stepsPerNotch, bool active)
 ^
In file included from src\ClickEncoder.cpp:12:0:
include/ClickEncoder.h:109:31: warning: 'ClickEncoder::accelerationEnabled' will be initialized after [-Wreorder]
   bool  accelerationEnabled = false;
                               ^
include/ClickEncoder.h:106:28: warning:   'volatile int16_t ClickEncoder::delta' [-Wreorder]
   volatile int16_t delta = 0;
                            ^
src\ClickEncoder.cpp:46:1: warning:   when initialized here [-Wreorder]
 ClickEncoder::ClickEncoder(uint8_t A, uint8_t B, uint8_t BTN, uint8_t stepsPerNotch, bool active)
 ^
In file included from src\ClickEncoder.cpp:12:0:
include/ClickEncoder.h:113:28: warning: 'ClickEncoder::button' will be initialized after [-Wreorder]
   volatile Button button = Open;
                            ^
include/ClickEncoder.h:110:19: warning:   'uint8_t ClickEncoder::steps' [-Wreorder]
   uint8_t steps = 0;
                   ^
src\ClickEncoder.cpp:46:1: warning:   when initialized here [-Wreorder]
 ClickEncoder::ClickEncoder(uint8_t A, uint8_t B, uint8_t BTN, uint8_t stepsPerNotch, bool active)
 ^
In file included from src\ClickEncoder.cpp:12:0:
include/ClickEncoder.h:110:19: warning: 'ClickEncoder::steps' will be initialized after [-Wreorder]
   uint8_t steps = 0;
                   ^
include/ClickEncoder.h:102:17: warning:   'const uint8_t ClickEncoder::pinA' [-Wreorder]
   const uint8_t pinA;
                 ^
src\ClickEncoder.cpp:46:1: warning:   when initialized here [-Wreorder]
 ClickEncoder::ClickEncoder(uint8_t A, uint8_t B, uint8_t BTN, uint8_t stepsPerNotch, bool active)
 ^
Compiling .pio\build\WANHAO_I3_MINI\src\Config.cpp.o
Compiling .pio\build\WANHAO_I3_MINI\src\DataStore.cpp.o
Compiling .pio\build\WANHAO_I3_MINI\src\DuetLaserSensor.cpp.o
Compiling .pio\build\WANHAO_I3_MINI\src\GCodes.cpp.o
Compiling .pio\build\WANHAO_I3_MINI\src\InputDialogs.cpp.o
Compiling .pio\build\WANHAO_I3_MINI\src\Menus.cpp.o
Compiling .pio\build\WANHAO_I3_MINI\src\SMuFF.cpp.o
Compiling .pio\build\WANHAO_I3_MINI\src\SMuFFtools.cpp.o
Compiling .pio\build\WANHAO_I3_MINI\src\SimpleGCodeParser.cpp.o
In file included from src\GCodes.cpp:28:0:
include/ZServo.h:73:12: error: 'uint32' does not name a type
   volatile uint32 *_pin_reg;
            ^
include/ZServo.h:74:3: error: 'uint32' does not name a type
   uint32 _pin_set;
   ^
include/ZServo.h:75:3: error: 'uint32' does not name a type
   uint32 _pin_reset;
   ^
include/ZServo.h:79:3: error: 'uint32' does not name a type
   uint32 _lastUpdate;
   ^
include/ZServo.h:80:12: error: 'uint32' does not name a type
   volatile uint32 _tickCnt;
            ^
src\GCodes.cpp: In function 'bool dummy(const char*, String, int)':
src\GCodes.cpp:114:9: warning: unused variable 'code' [-Wunused-variable]
     int code = buf.toInt();
         ^
In file included from src\SMuFF.cpp:23:0:
include/ZServo.h:73:12: error: 'uint32' does not name a type
   volatile uint32 *_pin_reg;
            ^
include/ZServo.h:74:3: error: 'uint32' does not name a type
   uint32 _pin_set;
   ^
include/ZServo.h:75:3: error: 'uint32' does not name a type
   uint32 _pin_reset;
   ^
include/ZServo.h:79:3: error: 'uint32' does not name a type
   uint32 _lastUpdate;
   ^
include/ZServo.h:80:12: error: 'uint32' does not name a type
   volatile uint32 _tickCnt;
            ^
src\GCodes.cpp: In function 'bool M98(const char*, String, int)':
src\GCodes.cpp:191:1: warning: no return statement in function returning non-void [-Wreturn-type]
 }
 ^
In file included from src\SMuFFtools.cpp:30:0:
include/ZServo.h:73:12: error: 'uint32' does not name a type
   volatile uint32 *_pin_reg;
            ^
include/ZServo.h:74:3: error: 'uint32' does not name a type
   uint32 _pin_set;
   ^
include/ZServo.h:75:3: error: 'uint32' does not name a type
   uint32 _pin_reset;
   ^
include/ZServo.h:79:3: error: 'uint32' does not name a type
   uint32 _lastUpdate;
   ^
include/ZServo.h:80:12: error: 'uint32' does not name a type
   volatile uint32 _tickCnt;
            ^
src\Menus.cpp: In function 'void setupMainMenu(char*)':
src\Menus.cpp:70:10: warning: unused variable 'items2' [-Wunused-variable]
     char items2[150];
          ^
src\Menus.cpp: In function 'void showOffsetsMenu(char*)':
src\Menus.cpp:989:9: warning: variable 'title' set but not used [-Wunused-but-set-variable]
   char* title;
         ^
src\SMuFFtools.cpp: In function 'bool setServoPos(int, int)':
src\SMuFFtools.cpp:1226:1: warning: control reaches end of non-void function [-Wreturn-type]
 }
 ^
*** [.pio\build\WANHAO_I3_MINI\src\SMuFF.cpp.o] Error 1
*** [.pio\build\WANHAO_I3_MINI\src\GCodes.cpp.o] Error 1
*** [.pio\build\WANHAO_I3_MINI\src\SMuFFtools.cpp.o] Error 1
=========================================================================================================== [FAILED] Took 6.03 seconds ===========================================================================================================

Environment       Status    Duration
----------------  --------  ------------
WANHAO_I3_MINI    FAILED    00:00:06.033
BIGTREE_SKR_MINI  IGNORED
===================================================================================================== 1 failed, 0 succeeded in 00:00:06.033 =====================================================================================================
The terminal process terminated with exit code: 1

Terminal will be reused by tasks, press any key to close it.

technik-gegg, 2019-12-10:
Yeah, sorry for that and for not seeing your post.

I've updated the source code.

Closed 2019-12-14.

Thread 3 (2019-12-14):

Is Ws2812b just optional?

NamkingWIN, 2019-12-14:
I see in the list of customized display board do not list ws2812b but in the schematic has one. Can I remove that on the oled board?

technik-gegg, 2019-12-14:
Yep, totally optional. It was meant to be used as an additional signalling feature but as of yet, the FastLED library does not compile on the STM32 environment.
Maybe some day in the future.

NamkingWIN, 2019-12-14:
Ok, can 2 resistor 10k also remove?

technik-gegg, 2019-12-14:
No. That one is needed for the encoder.

NamkingWIN, 2019-12-14:
Can you re-draw schematic exactly? Thanks!

Closed 2019-12-14.

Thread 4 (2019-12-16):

the display does not work

NamkingWIN, 2019-12-16:
Hi,
I have tried complied the firmware and flash it to SKR mini using stlinkV2 module. After that, I connect the oled lcd 0.96inch to skr (EXP1), the oled does not work, still dark. How can I check the SKR is still work properly?
Here is pic of my problem: https://app.box.com/s/7yo3w6t78riltsedot4lnrkzcf71cbjx
Thanks

technik-gegg, 2019-12-16:
There are a couple of methods you can try:
1. Connect a buzzer to it (EXP1/PC10). It'll play a tune on startup.
2. Connect a stepper motor to the Revolver. It's supposed to go to home position after startup. If you don't have an endstop on it, it'll turn infinitely. Trigger the endstop and it'll stop.
3. Start debugging the firmware from within PlatformIO and set a break point in setup(). It'll use the ST-Link to control/communicate.

Usually, if the programming was successful (SUCCESS response in PlatformIO) you have to check the wiring of your LCD. Since there are only 4 wires, of which 2 of them are powering the display you only have to check the SDA/SCL wires. Power wiring seems ok.

NamkingWIN, 2019-12-16:
I have debug and the result is below
`Processing BIGTREE_SKR_MINI (platform: ststm32; framework: arduino; board: genericSTM32F103RC)
--------------------------------------------------------------------------------
Verbose mode can be enabled via `-v, --verbose` option
CONFIGURATION: https://docs.platformio.org/page/boards/ststm32/genericSTM32F103RC.html
PLATFORM: ST STM32 5.7.0 > STM32F103RC (48k RAM. 256k Flash)
HARDWARE: STM32F103RCT6 72MHz, 48KB RAM, 256KB Flash
DEBUG: Current (stlink) External (blackmagic, jlink, stlink)
PACKAGES: toolchain-gccarmnoneeabi 1.70201.0 (7.2.1), framework-arduinoststm32-maple 1.10000.190819 (1.0.0)
LDF: Library Dependency Finder -> http://bit.ly/configure-pio-ldf
LDF Modes: Finder ~ chain, Compatibility ~ soft
Looking for U8G2 library in registry
Found: https://platformio.org/lib/show/942/U8g2
LibraryManager: Installing id=942
U8g2 @ 2.27.3 is already installed
Found 34 compatible libraries
Scanning dependencies...
Dependency Graph
|-- <SdFs> 2018.6.24
|   |-- <SPI> 1.0
|-- <ArduinoJson> 6.13.0
|-- <MemoryFree> #a2d60bd
|-- <U8g2> 2.27.3
|   |-- <SPI> 1.0
|   |-- <Wire> 1.0
|-- <SPI> 1.0
|-- <Wire> 1.0
Building in debug mode
Checking size .pio\build\BIGTREE_SKR_MINI\firmware.elf
Advanced Memory Usage is available via "PlatformIO Home > Project Inspect"
DATA:    [==        ]  22.1% (used 10856 bytes from 49152 bytes)
PROGRAM: [======    ]  63.5% (used 166460 bytes from 262144 bytes)
========================= [SUCCESS] Took 6.58 seconds =========================

Environment       Status    Duration
----------------  --------  ------------
WANHAO_I3_MINI    IGNORED
BIGTREE_SKR_MINI  SUCCESS   00:00:06.579
========================= 1 succeeded in 00:00:06.579 =========================
Reading symbols from d:\STL files\SMuFF+-+Smart+Multi+Filament+Feeder+with+#Bondtech+gears\SKR firmware\SMuFF-1.1\.pio\build\BIGTREE_SKR_MINI\firmware.elf...
done.
PlatformIO Unified Debugger -> http://bit.ly/pio-debug
PlatformIO: debug_tool = stlink
PlatformIO: Initializing remote target...
xPack OpenOCD, 32-bit Open On-Chip Debugger 0.10.0+dev (2019-07-17-07:34)
Licensed under GNU GPL v2
For bug reports, read
	http://openocd.org/doc/doxygen/bugs.html
hla_swd
Info : The selected transport took over low-level target control. The results might differ compared to plain JTAG/SWD
Info : tcl server disabled
Info : telnet server disabled
Info : clock speed 1000 kHz
Info : STLINK V2J34S7 (API v2) VID:PID 0483:3748
Info : Target voltage: 3.252695
Info : stm32f1x.cpu: hardware has 6 breakpoints, 4 watchpoints
Info : accepting 'gdb' connection from pipe
target halted due to debug-request, current mode: Handler External Interrupt(32)
xPSR: 0x01000030 pc: 0x08001654 msp: 0x2000be34
Info : device id = 0x10036414
Info : flash size = 256kbytes
0x08001654 in dma_clear_isr_bits (tube=DMA_CH5, dev=0x40004400) at C:\users\nguyen hoai nam\.platformio\packages\framework-arduinoststm32-maple\STM32F1\system\libmaple/stm32f1/include/series/dma.h:538
538	    dev->regs->IFCR = (1U << (4 * (tube - 1)));
target halted due to debug-request, current mode: Thread
xPSR: 0x01000000 pc: 0x080003f0 msp: 0x2000c000
Loading section .text, size 0x21bcc lma 0x8000000
Loading section .ARM.exidx, size 0x8 lma 0x8021bd0
Loading section .data, size 0x1218 lma 0x8021bd8
Loading section .rodata, size 0x5c4c lma 0x8022df0
Info : Padding image section 0 at 0x08021bcc with 4 bytes
target halted due to debug-request, current mode: Thread
xPSR: 0x01000000 pc: 0x08000454 msp: 0x2000c000
Start address 0x8000454, load size 166456
Transfer rate: 22 KB/sec, 12804 bytes/write.
target halted due to debug-request, current mode: Thread
xPSR: 0x01000000 pc: 0x08000454 msp: 0x2000c000
target halted due to debug-request, current mode: Thread
xPSR: 0x01000000 pc: 0x08000454 msp: 0x2000c000
Temporary breakpoint 1 at 0x8004882: file C:\users\nguyen hoai nam\.platformio\packages\framework-arduinoststm32-maple\STM32F1\cores\maple\main.cpp, line 38.
PlatformIO: Initialization completed
PlatformIO: Resume the execution to `debug_init_break = tbreak main`
PlatformIO: More configuration options -> http://bit.ly/pio-debug
Note: automatically using hardware breakpoints for read-only addresses.

Temporary breakpoint 1, main () at C:\users\nguyen hoai nam\.platformio\packages\framework-arduinoststm32-maple\STM32F1\cores\maple\main.cpp:38
38	    setup();
`

NamkingWIN, 2019-12-16:
Here is my process of program the SKR:
1. Compile the firmware using platformIO
2. Upload firmware using platformIO after compiled success.
 Are wrongs in my process?

technik-gegg, 2019-12-16:
Nothing wrong with this. As far as I can tell, firmware is working. Debugger has stopped in main(), which it usually does. If you step through, it'll call setup() next. Try to step through to **setupSteppers()** in setup(). If that's working, check wiring of the display or try a different one.

NamkingWIN, 2019-12-16:
Here is the message after compiled firmware
`Linking .pio\build\BIGTREE_SKR_MINI\firmware.elf
Building .pio\build\BIGTREE_SKR_MINI\firmware.bin
Checking size .pio\build\BIGTREE_SKR_MINI\firmware.elf
Advanced Memory Usage is available via "PlatformIO Home > Project Inspect"
DATA:    [==        ]  22.1% (used 10856 bytes from 49152 bytes)
PROGRAM: [======    ]  63.5% (used 166460 bytes from 262144 bytes)
============================================= [SUCCESS] Took 109.93 seconds =============================================

Environment       Status    Duration
----------------  --------  ------------
WANHAO_I3_MINI    IGNORED
BIGTREE_SKR_MINI  SUCCESS   00:01:49.926
============================================== 1 succeeded in 00:01:49.926 ==============================================

Terminal will be reused by tasks, press any key to close it.`

NamkingWIN, 2019-12-16:
And this is the message Upload firmware

`Executing task: C:\Users\Nguyen Hoai Nam\.platformio\penv\Scripts\platformio.exe run --target upload --environment BIGTREE_SKR_MINI <
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
NamkingWIN, 2019-12-16:
I have check the oled, it works fine with the wemos d1 mini using U8g2lib. But not work with SKR.

technik-gegg, 2019-12-16:
Check your wiring according these pictures.
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

NamkingWIN, 2019-12-16:
> Check your wiring according these pictures.
> 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
> 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

My wiring is the same with you.
https://app.box.com/s/cr6c3lm7raa5h316p43rlikrf52rujwb
https://app.box.com/s/z9n6lnp9wq1298xhezy7aitq3f5e1xou
https://app.box.com/s/0yzkiba4ywawvohywzupagmqm42uylwk

technik-gegg, 2019-12-16:
I don't see an SD-Card in your SKR. You have to copy the according configuration file (SMUFF.CFG) onto a SD-Card and stick that into the board. Otherwise it'll not  work as expected.

NamkingWIN, 2019-12-16:
> I don't see an SD-Card in your SKR. You have to copy the according configuration file (SMUFF.CFG) onto a SD-Card and stick that into the board. Otherwise it'll not work as expected.

Where can I get this file? I saw the SMUFF-DUET.CFG at the Config/SKR mini/. Is that file you mean?

technik-gegg, 2019-12-16:
Yep. Rename it to SMUFF.CFG after copying.

NamkingWIN, 2019-12-16:
> Yep. Rename it to SMUFF.CFG after copying.

OK, thanks. The Oled work well.
The speaker has loud at begin. But the revolver step just turn 1 circle and stop not turn infinitely as you said.!!!
Another problem: the rotary encoder not affect when I scroll it. I am using the breaked out rotary encoder (intergrated 2 resistor 10k) as pic below.
https://app.box.com/s/ob6rpv6b7imgurjk8l9m53c2j3s6pqn5
My wiring is:
CLK --> PC14
DT --> PC15
SW -->PC11
+ --> 5V
GND --> GND

technik-gegg, 2019-12-16:
Don't know. Please double check your wiring.

NamkingWIN, 2019-12-17:
I am check the wiring of encoder, just as your setup. And I also check the encoder work fine, switch button of encoder can reset the board but not affect when connected at right place. Some problem in compile firmware (pic below) may cause the error?
https://app.box.com/s/6xevlji548lz9mh2ejrs88wef4he3jln

technik-gegg, 2019-12-17:
Those are no errors, just warnings.

The code will compile and the encoder does work! If not, you did something wrong assembling it.

NamkingWIN, 2019-12-17:
I just wiring the oled, speaker, reset button, encoder and the step with driver. That is enough for testing of SKR work properly? Or must wiring more component? Maybe the revolver turn to reach to the endstop at the begin so encoder does not work temporarily, I thought that. Is that right?

NamkingWIN, 2019-12-18:
Here are my wiring, please look pic at link below
https://app.box.com/s/wpir4ybonsuonxbh78x09zpzzs0ubi81
With this wiring the oled, speaker and reset button work fine but the encoder not work.
At the begin, the step of revolver just turn only 1 round and stop. (you can see at video https://app.box.com/s/aadpcgdieynzhfc6mzdi0ohm14macqzj)
Please help me to check the error. Thanks so much.

NamkingWIN, 2019-12-19:
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

Enable revolver to using servo, oled indicate "reading config" and stop there. I have still collecting some items to assembly SMuFF but it will complete soon.
Can you add some message show on the oled for debuging or notice to user where error is occured?

technik-gegg, 2019-12-19:
If you get the "reading config", your SMuFF.cfg is corrupted. You probably missed a coma.
Open the file in an editor, copy & paste it in here: https://arduinojson.org/v6/assistant/
It'll tell you what's wrong with it. Correct it and try again.
Unless the config is not read fully, there's not much to say debug wise.

technik-gegg, 2019-12-19:
Closing this thread because it doesn't relate to the issue anymore.

Closed 2019-12-19.

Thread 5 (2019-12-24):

Maybe booting failed even oled show ready!

NamkingWIN, 2019-12-24:
Hi,
On the oled show “I ready” but at the left-down corner show “0” instead the free memory left. What I am getting error?
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

technik-gegg, 2019-12-24:
That's not an error, that's by design. The memory display reliably only works on the ATMega CPUs but not on STM32. Hence, this information has been replaced by the amount of filament feed on the SKR board.
It's all as it's supposed to be.

codycato, 2019-12-29:
I'm at the same point now. Long press doesnt work for me.

technik-gegg, 2019-12-29:
Well guys, again, check your wiring!

This is, what it's supposed to be:

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

I'm pretty sure you've left out some connections.

codycato, 2019-12-29:
In the pic you have of the lcd board. The  Rotary knob section...S1= pin 9/BT-ENC. And  S2= GND.

The pic above shows the opposite. I tried both but same results.

technik-gegg, 2019-12-29:
That doesn't matter at all. It's just a switch that shorts to GND. Will work either way.

technik-gegg, 2019-12-29:
Maybe the flat ribbon cable you're using to connect to the board sucks. Try replacing it.

codycato, 2019-12-29:
Yea I thought about that so i tried a secon ribbon and and also went straight dupont to the skr connector. I'll try another rotary encoder tomorrow.

As for the SMUFF.cfg parser check says valid but it never boots whenever I edit and save. Only works when I just rename your original file.

technik-gegg, 2019-12-29:
I've uploaded a CFG for the servo variant. Try this one.

What does the ArduinoJson assistant say about the Memory Pool Size for ESP32/ESP8266? It's supposed to be somewhere around 1764 bytes.

codycato, 2019-12-29:
I'm not at the computer right now but If I remember correctly it was +1800. Can you upload cfg servo for duet please.

technik-gegg, 2019-12-29:
Did that.

codycato, 2019-12-29:
Stuck at "reading config" with the file you just uploaded :(

technik-gegg, 2019-12-29:
Try a different SD-Card, formatted with standard FAT.

codycato, 2019-12-29:
Did that, still stuck. I only have 2 sdcard that can format with standard FAT

codycato, 2019-12-29:
This is so weird. The original SMUFF_DUET.CFG works when I rename it. But the new ones dont.

technik-gegg, 2019-12-29:
Yep, that's weird... I just did the same without any issues.

Closed 2019-12-30.

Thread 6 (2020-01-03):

firmware.bin

davidcgu, 2020-01-03:
Hello mate,

First of all wanted to thank you for your great job and sharing, thats really amazing!!!!!!

I'm on the way of building mine following your instructions however I have a small problem....

I ordered an SKR Mini which unfortunately the micro SD card reader is not working, I'm claming to te seller to get a replacement however this will take no less than a month what will delay a lot my follow up....

I have made the test with an ST-link and I'm able to load the bootloader and the firmware.bin for marlin and it works as I can see as result that boots fine with marlin screen on an 2004 LCD.

I have my controler board made and ready to test with I2C address 60, I have compiled and flashed on the same way I do with the maling firmware.bin but nothing is shown on the oled display afterwards.

I assume it does not work as is not able to read the config flle on the micro sd card.

I wonder if provisionally there is some way to configure some firm that I can modify directly on VS and compile and run away from the sd card to make it boot and make some first motion tests.

Thanks in advance for your attention.

Aps... Happy new year to everybody!!!!!!!

technik-gegg, 2020-01-03:
The only thing you can do without an SD-Card is to hard code all values into the **SMuFFConfig** structure in **SMuFF.h** and comment out the readConfig() function in SMuFF.cpp.
Be aware that while powered you can change the settings in the menus but they will disappear as you turn of the device.
Also, the last selected tool gets lost after a power cycle, which is usually stored on the SD-Card too.

As for the programming: You have to do it via the ST-Link (or "Upload" in VSCode / Platform.io), otherwise the starting address will be set wrong and the main routine may not get called. This will also overwrite the bootloader.
Also, with the SKR you're not able to use I2C for communication because the SKR has to be configured as master for the OLED.  For I2C communication you'll need to set it up as slave/servant, which would render the OLED unusable. You must user the serial connection.

davidcgu, 2020-01-03:
Great, for testing purposes will be fine for me until getting a new board, I should start writting at the standard address for the bootloader which I know it is 0x08000000.

I don't know why but have not being able to get st-link to work with VS while it works fine with St.link soft.

Regards

technik-gegg, 2020-01-04:
I needed to flash my ST-Link with the latest firmware before they got recognized by VSCode / openOCD.

davidcgu, 2020-01-04:
Thanks, my oled it's working know, so at least I know the board I made it's fine and will be ok to make some movement tests.

I already upgraded the firm of the ST-link to latest and still not recognized by VS.

I falshed with STM32 cube tool from ST-link starting on address 0x08000000 which is the one assigned originally for the bootloader and it's fine, the good point is that now I learn how to flash stock bootloader and marlin with the st-link so can recover the board to another use if required.

I have no idea how the system works and have a small question for you.... I have a BMG on direct drive and don't like the idea to move to bowden, my question is.... how exactly system works? there is a way that SMUFF does the load/unload and afterwards is disabled and works the direct drive extruder? should work both in paralel (smuff extruder and the one on direct drive)?

Thanks a lot for your time, much appreciated.

technik-gegg, 2020-01-04:
Great to hear it's working.

Yes, that's more or less the standard function. You connect all 3 steppers (or 2 and the servo) to it, configure such parameters as bowden tube length and the SMuFF will do exactly this on a Tx command.
It'll retract the current filament, change the Selector position, load the new filament and then release the filament (i.e. move the Revolver to home or open the servo). From there, your direct drive extruder has to take over and feed to nozzle.
That's the way the Prusa MMU does it and it also has some remarkable changes in their printers firmware as well to accomplish this task. For example: They order the MMU to feed filament until the filament sensor of the extruder triggers, then the printer send an **Abort** command. This makes it easier to handle when the bowden tube length changes but you need far more integration work on the printers firmware side.

As I've already stated a couple of times: The major culprit here is that you have to feed the filament through one more set of gears. As you know, BMG has very tight tolerances and the only way to feed some bulged filament into it is: Not to have bulged filament! Means, you have to experiment a bit with filament tip shaping techniques.

That's one of the main reasons I'm recommending the bowden system.

The other reason is: If you don't have a BMG direct drive system (i.e. something  MK8-ish), it doesn't make much sense going from the SMuFF BMG gears to something weaker and less reliable.
But that's just my recommandation and nothing that's carved in stone.

Closed 2020-01-06.

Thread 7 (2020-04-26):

[idea] klipper

Dario-Ciceri, 2020-04-26:
I would like to use this system on a voron 2.4 running klipper with a duet wifi. I will connect the motors and the endstop for this machine to my duet expansion board and I'm wondering if is it possible to use klipper to control this... I can't try this out now because I don't own this machine and I don't have a Voron but after that I'll try

technik-gegg, 2020-04-26:
Well, I'm not sure why one would use Klipper on a Duet WiFi.
As far as I understand Klipper, it was meant to overcome the restrictions you'll get on an 8-Bit controller board, which is not being able to handle GCode at higher print speeds.
Klipper is based on the Raspberry, which is 32-Bit and thus has much more computing power than the average 8-Bit printer controller.

The Duet boards already are equipped with 32-Bit controllers and they do have the power to print with higher speeds right away.

That being said, as you plan to control the SMuFF hardware all through Klipper and the Duex, it sure is possible. You only have to set up your Klipper scripts so that they go through all the necessary steps to accomplish a tool change (i.e unload filament, move selector, load new filament).

Dario-Ciceri, 2020-04-26:
raspberry is 64bit too but that doesn't matter cause yes it's true I don't need to use klipper and multicolor/filament is a better choice at the moment

technik-gegg, 2020-04-26:
Just one thing you may have to take into consideration as we're talking of speed:
On my machines I'm able to print reliable with speeds up to 180mm/s. Everything that goes beyond will cause under extrusion because the extruder is not able to cope with higher speeds than that and I'm talking about Bondtech extruders.
So, even if you're able to speed computing up with 64-Bit, you'll still face the extrusion problem unless you use a completely different extrusion system.

So, If you want to drive the SMuFF without its controller but only via the Duet/Duex w/o Klipper, there're some guys who did that already. Head over to [this remix](https://www.thingiverse.com/thing:4208998) and see if that's of any use for you.
You might need to ask Codycato for his (Duet) scripts directly, since I'm not sure he published them.

Dario-Ciceri, 2020-04-26:
Don't worry I changed idea cause I figured out that I can't use smuff with directdrive and I want directdrive so I'll put smuff on my second printer which I use for mod testing 😄
Thank you I'll let you know when I'll try on my hevo!!!

Closed 2020-04-26.

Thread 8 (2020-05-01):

Compatible LCDs and support for NUCLEO-F103RB

sl1pkn07, 2020-05-01:
Hi

im looking and buy the pieces for mount this awesome project!

but i have a lite questions

what type of LCDs is compatible with Smuff?

can work with SPI displays like the CR10/ENDER3 display? (10wires, display+encoder) (i have one wothout use)

if only use I2C, this display can work? https://es.aliexpress.com/item/32853228170.html (editer, the other display is SPI (damm SDA name XD))
0.9" is little small for me (and +2" is quite expensive)

my project is based on ST NUCLEO-F103RB+CNC shield

greetings

technik-gegg, 2020-05-02:
Since you planning not to use an aftermarket controller (i.e. SKR mini) but the Nucleo development board, you can use pretty much any display you pick.
Though, you have to check beforehand whether or not the display controller you pick is supported by the [U8G2 library](https://github.com/olikraus/u8g2/wiki) from Oliver Kraus, since this is the one the SMuFF firmware builds upon.
If it does, you only have to initialize the correct display (controller type) in SMuFF.cpp.
I'd say, chances are pretty good you'll be able to reuse your CR10 display (aka standard RepRap 12864 display).

I've used the I2C OLED for two reasons:
1. The SKR mini on board display connectors are driven through the SPI3 interface. U8G2 doesn't support this interface directly (only SPI1 and SPI2 in some cases).
This would have required to clone the library and patch it where needed, which is somehow neglecting the meaning of a "standard library".
2. The I2C OLED is pretty easy to integrate (4 pins only). Sure, it's physical size (0.9" or 1.3") isn't huge but it comes with a decent resolution of 128 x 64 px.
In case of the SMuFF controller the physical size doesn't matter much, since you'll not be doing something major with it most of the time. It's being used only for setup and some status information display.

sl1pkn07, 2020-05-02:
Hi

the TFT i posted use the SSD1327 controller, and seems is supported by U8G2

i use the nucleo because have the same family of MCU (STM32F103XXX6) and i have already one

thanks

PD: a litle offtopic. you know this board?

https://wiki.fysetc.com/AIO_II/
https://github.com/FYSETC/AIO_II

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

i think is perfect for you project. have 4 drivers (exist a module for 4xTMC2208 in UART), have integrated LCD, encoder, SD and reset button. also have a free Serial pin header (include I2C pinout)

technik-gegg, 2020-05-02:
Yes, the display is supported although, it's got twice the resolution in height (128px), so you might need to modify some of the screens of the SMuFF firmware.

The FYSETC controller is nice! Great find.
It's a combination of the Wanhao i3 mini (first controller of the SMuFF) and the SKR - I might want one ;o)

sl1pkn07, 2020-05-02:
i have one, but i want to use for other project (DVD drive printer). sadly the missing servo. i'm not sure if can be used the fancy RGB port)

greetings

technik-gegg, 2020-05-02:
You can use the RGB if you get access to the signal before the MOSFETS.
That's the price you pay for highly integrated stuff...

sl1pkn07, 2020-05-10:
Hi, sorry for hihacked my own thread, bit i need little help with support for Nucleo-f103rb

<details>

~~~patch
diff --git a/Configs/NUCLEO_F103RB/SMUFF_Duet.CFG b/Configs/NUCLEO_F103RB/SMUFF_Duet.CFG
new file mode 100644
index 0000000..39770dc
--- /dev/null
+++ b/Configs/NUCLEO_F103RB/SMUFF_Duet.CFG
@@ -0,0 +1,70 @@
+{
+   "Serial1Baudrate":  56700,
+   "Serial2Baudrate":  56700,
+   "SerialDueBaudrate": 56700,
+   "ToolCount":                   5,
+   "BowdenLength":             620.0,
+   "SelectorDist":      34.0,
+   "LCDContrast":              190,
+   "I2CAddress":                  136,
+   "MenuAutoClose":       20,
+   "FanSpeed":                         50,
+   "DelayBetweenPulses": false,
+   "PowerSaveTimeout":         300,
+   "Duet3DDirect":      true,
+   "EmulatePrusa":      false,
+   "UnloadCommand":     "",
+
+   "Selector": {
+      "Offset": 0.5,
+      "Spacing": 21.0,
+      "StepsPerMillimeter": 80,
+          "Acceleration": 12000,
+          "MaxSpeed":  2000,
+          "MaxSpeedHS":  2500,
+          "InvertDir": false,
+          "EndstopTrigger": 1,
+      "StepDelay": 10
+   },
+   "Revolver": {
+          "StepsPerRevolution": 9600,
+      "Offset": 1275,
+          "Acceleration": 22000,
+          "MaxSpeed":  10000,
+          "ResetBeforeFeed": true,
+          "HomeAfterFeed": false,
+          "InvertDir": false,
+          "EndstopTrigger": 1,
+      "StepDelay": 5,
+      "Wiggle": false,
+      "UseServo": false,
+      "ServoOffPos": 30,
+      "ServoOnPos": 90
+   },
+   "Feeder": {
+          "ExternalControl": true,
+      "StepsPerMillimeter": 410,
+          "Acceleration": 20000,
+          "MaxSpeed":  1400,
+          "InsertSpeed": 20000,
+          "ReinforceLength": 0,
+      "UnloadRetract": 0,
+          "UnloadPushback": 0,
+          "PushbackDelay": 2.0,
+          "InvertDir": true,
+          "EndstopTrigger": 1,
+      "StepDelay": 3,
+      "EnableChunks": false,
+      "FeedChunks": 20,
+          "InsertLength": 5,
+      "DuetLaser": false
+   },
+   "Materials": {
+      "T0": "PLA Green",
+      "T1": "PLA White",
+      "T2": "PLA Red",
+      "T3": "PLA Black",
+      "T4": "PLA Silver"
+   }
+}
+
diff --git a/Configs/NUCLEO_F103RB/SMUFF_PMMU.CFG b/Configs/NUCLEO_F103RB/SMUFF_PMMU.CFG
new file mode 100644
index 0000000..9725a21
--- /dev/null
+++ b/Configs/NUCLEO_F103RB/SMUFF_PMMU.CFG
@@ -0,0 +1,71 @@
+{
+   "Serial1Baudrate":  56700,
+   "Serial2Baudrate":  56700,
+   "SerialDueBaudrate": 56700,
+   "ToolCount":                   5,
+   "BowdenLength":             620.0,
+   "SelectorDist":      34.0,
+   "LCDContrast":              190,
+   "I2CAddress":                  136,
+   "MenuAutoClose":       20,
+   "FanSpeed":                         50,
+   "DelayBetweenPulses": false,
+   "PowerSaveTimeout":         300,
+   "Duet3DDirect":      false,
+   "EmulatePrusa":      true,
+   "UnloadCommand":     "",
+
+   "Selector": {
+      "Offset": 0.5,
+      "Spacing": 21.0,
+      "StepsPerMillimeter": 80,
+          "Acceleration": 12000,
+          "MaxSpeed":  2000,
+          "MaxSpeedHS": 2500,
+          "InvertDir": false,
+          "EndstopTrigger": 1,
+      "StepDelay": 10
+   },
+   "Revolver": {
+          "StepsPerRevolution": 9600,
+      "Offset": 1275,
+          "Acceleration": 22000,
+          "MaxSpeed":  10000,
+          "ResetBeforeFeed": true,
+          "HomeAfterFeed": true,
+          "InvertDir": false,
+          "EndstopTrigger": 1,
+      "StepDelay": 5,
+      "Wiggle": false,
+      "UseServo": false,
+      "ServoOffPos": 30,
+      "ServoOnPos": 90
+   },
+   "Feeder": {
+          "ExternalControl": true,
+      "StepsPerMillimeter": 410,
+          "Acceleration": 20000,
+          "MaxSpeed":  1400,
+          "InsertSpeed": 20000,
+          "ReinforceLength": 0,
+      "UnloadRetract": 0,
+          "UnloadPushback": 0,
+          "PushbackDelay": 2.0,
+          "InvertDir": true,
+          "EndstopTrigger": 1,
+      "StepDelay": 3,
+      "EnableChunks": false,
+      "FeedChunks": 20,
+          "InsertLength": 5,
+      "DuetLaser": false
+
+   },
+   "Materials": {
+      "T0": "PLA Green",
+      "T1": "PLA White",
+      "T2": "PLA Red",
+      "T3": "PLA Black",
+      "T4": "PLA Silver"
+   }
+}
+
diff --git a/Configs/NUCLEO_F103RB/SMUFF_Servo.CFG b/Configs/NUCLEO_F103RB/SMUFF_Servo.CFG
new file mode 100644
index 0000000..b26d3a0
--- /dev/null
+++ b/Configs/NUCLEO_F103RB/SMUFF_Servo.CFG
@@ -0,0 +1,71 @@
+{
+   "Serial1Baudrate":  56700,
+   "Serial2Baudrate":  56700,
+   "SerialDueBaudrate": 56700,
+   "ToolCount":                   5,
+   "BowdenLength":             620.0,
+   "SelectorDist":      34.0,
+   "LCDContrast":              190,
+   "I2CAddress":                  136,
+   "MenuAutoClose":       20,
+   "FanSpeed":                         50,
+   "DelayBetweenPulses": false,
+   "PowerSaveTimeout":         300,
+   "Duet3DDirect":      false,
+   "EmulatePrusa":      true,
+   "UnloadCommand":     "",
+
+   "Selector": {
+      "Offset": 0.5,
+      "Spacing": 21.0,
+      "StepsPerMillimeter": 80,
+          "Acceleration": 12000,
+          "MaxSpeed":  2000,
+          "MaxSpeedHS": 2500,
+          "InvertDir": false,
+          "EndstopTrigger": 1,
+      "StepDelay": 10
+   },
+   "Revolver": {
+          "StepsPerRevolution": 9600,
+      "Offset": 1275,
+          "Acceleration": 22000,
+          "MaxSpeed":  10000,
+          "ResetBeforeFeed": true,
+          "HomeAfterFeed": true,
+          "InvertDir": false,
+          "EndstopTrigger": 1,
+      "StepDelay": 5,
+      "Wiggle": false,
+      "UseServo": true,
+      "ServoOffPos": 30,
+      "ServoOnPos": 90
+   },
+   "Feeder": {
+          "ExternalControl": true,
+      "StepsPerMillimeter": 410,
+          "Acceleration": 20000,
+          "MaxSpeed":  1400,
+          "InsertSpeed": 20000,
+          "ReinforceLength": 0,
+      "UnloadRetract": 0,
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
technik-gegg, 2020-05-10:
I don't think you'll get it 320 bytes down removing the JSON parser.
I'd rather say, shorten the texts in String.h, since those will be put into the ROM section as well.

To get rid of the JSON parser, you have to put your values as defaults into the smuffConfig structure in SMuFF.h and comment out the code in Config.cpp.

sl1pkn07, 2020-05-10:
with

~~~patch
diff --git a/include/SMuFFBitmaps.h b/include/SMuFFBitmaps.h
index a2ac3cd..42028e6 100644
--- a/include/SMuFFBitmaps.h
+++ b/include/SMuFFBitmaps.h
@@ -22,7 +22,11 @@

 #define logo_width  128
 #define logo_height 64
-static const unsigned char logo_bits[] PROGMEM = {
+#ifdef __BRD_NUCLEO_F103RB
+  static const unsigned char logo_bits[] PROGMEM = {
+  0x00, };
+#else
+  static const unsigned char logo_bits[] PROGMEM = {
   0x00, 0x00, 0xE0, 0xFF, 0x07, 0x00, 0x00, 0x00, 0x00, 0x00, 0x00, 0x00,
   0x00, 0x00, 0x00, 0x00, 0x00, 0x00, 0xFC, 0xFF, 0x1F, 0x00, 0x00, 0x00,
   0x00, 0x00, 0x00, 0x00, 0x00, 0x00, 0x00, 0x00, 0x00, 0x80, 0x7F, 0x00,
@@ -109,5 +113,5 @@ static const unsigned char logo_bits[] PROGMEM = {
   0x00, 0x00, 0x00, 0x00, 0x00, 0x00, 0x00, 0x00, 0x00, 0x00, 0x00, 0x00,
   0x00, 0x00, 0x00, 0x00, 0x00, 0x00, 0x00, 0x00, 0x00, 0x00, 0x00, 0x00,
   0x00, 0x00, 0x00, 0x00, };
-
+  #endif
 #endif
diff --git a/src/SMuFF.cpp b/src/SMuFF.cpp
@@ -109,5 +113,5 @@ static const unsigned char logo_bits[] PROGMEM = {
   0x00, 0x00, 0x00, 0x00, 0x00, 0x00, 0x00, 0x00, 0x00, 0x00, 0x00, 0x00,
   0x00, 0x00, 0x00, 0x00, 0x00, 0x00, 0x00, 0x00, 0x00, 0x00, 0x00, 0x00,
   0x00, 0x00, 0x00, 0x00, };
-
+  #endif
 #endif
~~~

~~~
Checking size .pio/build/NUCLEO_F103RB/firmware.elf
Advanced Memory Usage is available via "PlatformIO Home > Project Inspect"
RAM:   [=====     ]  53.9% (used 11032 bytes from 20480 bytes)
Flash: [==========]  99.5% (used 130368 bytes from 131072 bytes)
================================================================================================================== [SUCCESS] Took 4.79 seconds ==================================================================================================================

Environment       Status    Duration
----------------  --------  ------------
WANHAO_I3_MINI    IGNORED
BIGTREE_SKR_MINI  IGNORED
NUCLEO_F103RB     SUCCESS   00:00:04.785
================================================================================================================== 1 succeeded in 00:00:04.785 ==================================================================================================================
~~~

should be ok?

technik-gegg, 2020-05-10:
WTF?

technik-gegg, 2020-05-10:
Well, ok ;o)

sl1pkn07, 2020-05-10:
the code is not for merge to upstream, so don't worry xd

sl1pkn07, 2020-05-13:
well, the branch experimental overflow the nucleo by 1264 bytes

well, time to mod the nucleo! (STM32F103RET6 incoming!)

Closed 2020-05-17.

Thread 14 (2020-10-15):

SMuFF on Klipper and V5 build

flopana77, 2020-10-15:
Hi technik-geeg
I am a looking at running the SMuFF via Klipper. That said, I wanted to build the V5 and didn't put my mail address in the donation...Is there any way we can get in contact regarding the stl-files and to discuss the Klipper implementation later on?
Cheers
PS: Sorry for contacting this way...didn't figure any other option...

flopana77, 2020-10-15:
Once the build is ready to tackle Klipper, we'll talk again 👍

technik-gegg, 2020-10-15:
We'll do.

Closed 2020-10-15.

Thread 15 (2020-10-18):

Cannot compile Fysetc AIO II version

oengst, 2020-10-18:
Hello,

today I tried to compile the firmware for the Fysetc AIO II board.

When I try to compile it I get some errors about some settings not being defined.

`src\GCodes.cpp: In function 'bool M569(const char*, String, int)':
src\GCodes.cpp:1541:26: error: 'STALL_X_PIN' was not declared in this scope
         if(param == 0 && STALL_X_PIN != -1)

                          ^~~~~~~~~~~
src\GCodes.cpp:1546:12: error: 'STALL_X_PIN' was not declared in this scope
         if(STALL_X_PIN != -1)

            ^~~~~~~~~~~
src\GCodes.cpp:1558:26: error: 'STALL_Y_PIN' was not declared in this scope
         if(param == 0 && STALL_Y_PIN != -1)

                          ^~~~~~~~~~~
src\GCodes.cpp:1563:12: error: 'STALL_Y_PIN' was not declared in this scope
         if(STALL_Y_PIN != -1)

            ^~~~~~~~~~~
src\GCodes.cpp:1575:26: error: 'STALL_Z_PIN' was not declared in this scope
         if(param == 0 && STALL_Z_PIN != -1)

                          ^~~~~~~~~~~
src\GCodes.cpp:1580:12: error: 'STALL_Z_PIN' was not declared in this scope
         if(STALL_Z_PIN != -1)

            ^~~~~~~~~~~
src\GCodes.cpp: In function 'bool M914(const char*, String, int)':

src\GCodes.cpp:1728:12: error: 'STALL_X_PIN' was not declared in this scope

         if(STALL_X_PIN != -1)

            ^~~~~~~~~~~
src\GCodes.cpp:1733:12: error: 'STALL_X_PIN' was not declared in this scope
         if(STALL_X_PIN != -1)

            ^~~~~~~~~~~
src\GCodes.cpp:1749:12: error: 'STALL_Y_PIN' was not declared in this scope
         if(STALL_Y_PIN != -1)

            ^~~~~~~~~~~
src\GCodes.cpp:1754:12: error: 'STALL_Y_PIN' was not declared in this scope
         if(STALL_Y_PIN != -1)

            ^~~~~~~~~~~
src\GCodes.cpp:1770:12: error: 'STALL_Z_PIN' was not declared in this scope
         if(STALL_Z_PIN != -1)

            ^~~~~~~~~~~
src\GCodes.cpp:1775:12: error: 'STALL_Z_PIN' was not declared in this scope
         if(STALL_Z_PIN != -1)

            ^~~~~~~~~~~
*** [.pio\build\FYSETC_AIOII_SD\src\GCodes.cpp.o] Error 1`

Am I missing a setting or is that an issue with the project?

Thanks a lot.

technik-gegg, 2020-10-19:
You're not missing anything, that's a bug!

Please add these lines to  the **Pins.h** for the FYSETC_AIOII:
```
#define USB_CONNECT_PIN     -1
#define SD_DETECT_PIN       -1

#define STALL_X_PIN         -1
#define STALL_Y_PIN         -1
#define STALL_Z_PIN         -1
```
Also, in order to compile successfully, please modify your **platformio.ini** and add the "# add this" lines:

```
[env:FYSETC_AIOII_SD]
platform         = ststm32
framework        = arduino
board            = genericSTM32F103RC
board_build.core = maple
lib_deps         = ${common.lib_deps}
                  # add this
                   ${TMC.lib_deps}

build_flags      = ${common.build_flags}
                   ${USB.build_flags}
                 # add this
                   ${TMC.build_flags}

                   -I include/FYSETC_AIOII
                   -D __BRD_FYSETC_AIOII
                   -D __STM32F1__
                   -D USE_RGB_BACKLIGHT
build_unflags    = ${common.build_unflags}
extra_scripts    = include/FYSETC_AIOII/FYSETC_AIOII_SD.py
```

I will correct this for 2.12.

oengst, 2020-10-19:
Hi,

thanks for the information.
With that data I am able to compíle it. I still have an issue uploading it to the device but that might be related to my PlatformIO setup.

The upload via SD card is not doing anything.
So I downloaded the STM32Flash tool .
If I use that one it stops with the information: "Program Space Must In either (0x08000000-0x0807FFFF) or (0x20000000-0x2000FFFF)"

`DTR be Low(-3--12V),Reset
RTS be High(+3-+12V),enter ISP
...Delay 100ms
DTR be High(+3-+12V),Reset Released
RTS keep High
Connectting...4, Received:79 1F
Connect Ok @COM3@460800bps,@641ms
BootLoader Version:2.2
PID:00000414  STM32F10xxx_High-density
OptionBytes readout:
A55AFF00FF00FF00FF00FF00FF00FF00
96bit unique device ID:
[38FFDC05504D333238850243]
[05DCFF38 32334D50 43028538]
FLASH ROM size:256KB
SRAM size:65535KB(For reference only!!!)
Program Space Must In either (0x08000000-0x0807FFFF) or (0x20000000-0x2000FFFF)
`

That looks like the python scripts in the include folder are not running. So I tried to run external (as a newbie to python) but it fails on the

`Import("env")`

line. Research in internet did not reveal to me what I need to use to make imports work that way.

Maybe you can help me with a hint to get around this?

Thanks  a lot.

technik-gegg, 2020-10-19:
Be careful with the Flash tool. If not configured properly, it might erase your bootloader!

All environments named **_SD** are supposed to be flashed using the SD-Card.
Copy the **firmware.bin** file from the **SMuFF\.pio\build\FYSETC_AIOII_SD** folder onto the SD-Card, insert it into the AIOII, reset the device and wait a couple of seconds.
Please notice that, after the firmware is being flashed, the SMuFF will start up and try to read the SMUFF.CFG file from the SD-Card. So you have to copy that one as well.

Just for reference: [Compile the firmware](https://sites.google.com/view/the-smuff/how-to/tutorials/compile-the-firmware
)

oengst, 2020-10-20:
Thanks for your support.

I was now able to compile the firmware from the experimental branch and upload it to the board. I just needed to flash the original bootloader from board manufacturer since there was already a Marlin on the device when I bought it.
And that did obviously not upload a new firmware.bin when available at startup.

Is it mandatory to have everything wired up to be able to do anything in the smuff controller?

My actualy situation is like in this private shared video (only available with link)

https://www.youtube.com/watch?v=wIhndu7ZMWw

After starting it does some beeps, reads the configuration and then opens settings. After that it stops doing anything. No reaction on controller turn or click.

Would it be easier if I use a kind of "standard set" to wire the Smuff up? Which board would that be? Would that make things easier for me?

Thanks a lot.

technik-gegg, 2020-10-21:
Yeah, that seems to be an odd issue on the AIOII.
Maker @sl1pkn07 found out, that the encoder needed additional [pull-up resistors on the encoder pins](https://github.com/technik-gegg/SMuFF-1.1/pull/11#issuecomment-649840817) to make that thing work.

Well, for the start all you need is the board, display, SD-Card and firmware but you won't be able to do much, except changing the settings. If you want to play around, I'd recommend connecting at least two stepper motors (X and Z), two endstops (for X and Z) and one servo.
Also, I'd recommend using a USB to TTL serial interface and connecting the it to the SMuFF, so you can control it via a terminal app by [sending GCodes](https://sites.google.com/view/the-smuff/tips-hints/talk-to-the-smuff?authuser=0).

> Would it be easier if I use a kind of "standard set" to wire the Smuff up? Which board would that be? Would that make things easier for me?

Not sure what you mean by "standard set"...

sl1pkn07, 2020-10-25:
tested in my unit (with pullups in the enc pins). same problem like @oengst  (freeze in the settting menu)

about this board, by default comes without bootloader, you must burn it (the bootloader) before use the flash by SD feature

greetings

oengst, 2020-10-26:
> Not sure what you mean by "standard set"...

I wonder which is the newest board / screen combination that is supported and known as working perfectly.

Thanks :-)

technik-gegg, 2020-10-27:
Oh... that.
Well, there's not much of a choice here. The initial (2.x) board, the SKR mini V1.1 isn't available anymore (or at least hard to get). So, you'll probably go for the SKR E3 DIP (V1.1).
Basically, all SKR E3 versions are supported (E3 - **not DIP** - V1.2 and V2.0).  Though, with the V1.2 and 2.0 you'll get all the stepper drivers soldered directly onto the board, so there's not much room to tinker with.

As for the display: I myself still prefer the [DIY OLED](https://sites.google.com/view/the-smuff/how-to/tutorials/build-the-custom-display?authuser=0) solution over all others.
In the next release of the firmware, [this OLED module](https://sites.google.com/view/the-smuff/work-in-progress?authuser=0#h.1efg2hp8wplx) will be supported as well. Beside a few buttons more, this comes with the advantage of a 1.3" display which is easier to read and you won't have to DIY.

sl1pkn07, 2020-11-16:
as note. the version 2.09 is the latest version that works with the AIO unit. but need a little tweak not added in the code in that version

~~~
diff --git a/src/SMuFF.cpp b/src/SMuFF.cpp
index 37cfee7..9d6b0b1 100644
--- a/src/SMuFF.cpp
+++ b/src/SMuFF.cpp
@@ -306,6 +306,12 @@ void initFastLED() {
 void setup() {

 #ifdef __STM32F1__
+
+  // Disable JTAG pins for use in general purposes
+  #ifdef __BRD_FYSETC_AIOII
+    disableDebugPorts();
+  #endif
+
   #ifndef USE_TWI_DISPLAY
     #ifdef STM32_REMAP_SPI
     afio_remap(AFIO_REMAP_SPI1);  // remap SPI3 to SPI1 if a "normal" display is being used

~~~

also, the LCD color sequence not work al all:

Menu            Real Color
Cyan       ->  Blue
Magenta ->  Magenta
Yellow     ->  Cyan
White     ->  White
Black      ->  Black (no backligth)
Red        ->  Red
Green    ->  Green
Blue       ->  Yellow

greetings

technik-gegg, 2020-11-17:
Thank you Gustavo.
I'll add the SPI remapping back in 2.14 and correct the color settings.

Closed 2020-11-03.

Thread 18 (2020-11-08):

TWI problem

luismello, 2020-11-08:
After turn ON, it has continuous beep, I checked and the file size is 2200, but the SMUFF.CFG file has 2378, I changed the file size limit and Smuff turn ON.

But the Main Menu doesn't appear.

technik-gegg, 2020-11-09:
Have you read the [README of this release](https://github.com/technik-gegg/SMuFF-1.1/tree/SMuFF-2.0-(Experimental)#recent-changes)? There have been a lot of changes for menus and config files.

luismello, 2020-11-09:
hi

I put Menus, Options and Sound, but the menus still have a problem

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

technik-gegg, 2020-11-10:
I'm working on it, please stay tuned.

Nice wiring btw. so... colorful ;o)

luismello, 2020-11-10:
Hi TG

I will buy the BTT Mini12864 V1.0.

I did with the threads I had at home, hehe

technik-gegg, 2020-11-11:
@luismello
Checked in 2.13. Please try it and let me know if there are still issues.

luismello, 2020-11-14:
Hi TG

Version 2.13 did not solve my problem with Oled.

technik-gegg, 2020-11-15:
Is your OLED basically working and has a distorted screen or does it freeze up at some point?

Closed 2020-12-22.

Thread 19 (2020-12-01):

Not working with SKR mini E3 V1.2

nasrabq, 2020-12-01:
It build successfully but when flashing it to SKR mini E3 V1.2 using the SD card, the LCD shows only backlight.
I am using the Creality LCD, I have verify that both the mainboard and the LCD are working as I upload Marlin software and they are working OK.
I have changed the display in Platformio.ini and then build the BIGTREE_SKR_MINI_E3_SD, is there anything I missed?

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

technik-gegg, 2020-12-01:
Which firmware version have you been using?

nasrabq, 2020-12-01:
I am using SMuFF-1.1-SMuFF-2.0-Experimental

technik-gegg, 2020-12-01:
Yeah, that's for sure.
What does the Config.h say?
Also, do you hear a tune (melody) after startup?
And, last but not least, have you copied all the files and folders to the SD-Card as well?

nasrabq, 2020-12-01:
What does the Config.h say? **I have not change anything in this, it is the same as downloaded.**
Also, do you hear a tune (melody) after startup? **No sound at all**
And, last but not least, have you copied all the files and folders to the SD-Card as well? **I copied the configuration files from \Configs\SKR_mini folder only, do I need to copy other files**

technik-gegg, 2020-12-01:
In the Config.h is the latest VERSION string.
Yes, you do, [have a look](https://discordapp.com/channels/741179485474521110/742611826264506368/780830875582464070) (which is btw. also described in the README.md).

nasrabq, 2020-12-01:
VERSION_STRING    "V2.13"
I have copied the below folders in the SD card:
- help
- menus
- options
- sounds
- test

also copied the below files:

- firmware.bin
- MATERIALS.CFG
- SERVOMAP.CFG
- SMUFF.CFG
- TMCDRVR.CFG

but still did not get anything in the LCD also no sound

technik-gegg, 2020-12-01:
ok, the reason is: You need VERSION 2.14 (which is the latest published).

Be aware that you might not be able to select any menu item because the encoder button seems not to be working on some Creality displays (without modification). It does work on mine (original Ender-3 Pro display) but I've been told there are some out there who don't.

nasrabq, 2020-12-01:
Thank you, It is working now.

technik-gegg, 2020-12-01:
The encoder button as well?

nasrabq, 2020-12-01:
Yes, the encoder button is working

technik-gegg, 2020-12-01:
Good to know. Thanks!

nasrabq, 2020-12-01:
I have another issue with the display, It looks unreadable:
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

technik-gegg, 2020-12-01:
You're the second one having this issue...

I'm not quite sure, but I'm pretty convinced that this issue relates to your SD-Card. Menus and options will be read from SD-Card (hence you had to copy the folders). I bet the start screen on your display looks pretty normal!?

Can you format your SD-Card and give it another try (or better yet, use a fresh one).

nasrabq, 2020-12-02:
I have tested the with multiple SD-Cards but all not displaying anything and multiple sizes (128MB, 1GB and 8GB)
I have flashed Marlin and the SD-Card working OK, I can see the STL files in the SD-Card.

technik-gegg, 2020-12-02:
Ok, I'm stumped. I can't reproduce that with my  equipment. What about the main screen and the tools menu, are they showing correctly?

nasrabq, 2020-12-02:
I reflash it and now shows nothing, the firmware isflashed but because the menus is in the SD it is not displayed

technik-gegg, 2020-12-02:
Make sure you don't have copied the config files from 2.13, they don't work anymore.
At this stage it's hard to tell what went wrong. The only way to check is to connect the controller via TTL to USB on TFT connector to the PC and watch the debug outputs in a terminal app ([here's the how to](https://sites.google.com/view/the-smuff/tips-hints/talk-to-the-smuff?authuser=0)).

technik-gegg, 2020-12-06:
Good news! Found a bug in my .editorconfig file.

The .editorconfig of the SMuFF-Project needs to be set to:
```
[*.mnu, *.opt]
charset = utf-8
end_of_line = crlf
```

Please change it manually or get the latest version from my Github repository and make sure that your **.mnu** and **.opt** files on the SD-Card are ending with CR + LF (_0D 0A_) instead of LF only (_0A_). You may have to use a HEX-Editor to check the files.
Otherwise the loadMenu function will not parse the files correctly and thus menus will look pretty much distorted.

technik-gegg, 2020-12-08:
I have to correct myself.
Obviously this was not the cause for this kind of error. There's now a new FW version (2.16) released, which compiles against the STM32 V10.0.1 framework. This framework has got some fundamental changes in the SD-Card Library (most probably introduced already in V9.0.0), which might explain this strange behavior.
Please use the latest version and tell me whether or not this neutralizes the "faulty display" error.

Closed 2020-12-06.

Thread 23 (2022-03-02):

Klipper via macros and shell commands?

Alfiegerner, 2022-03-02:
Hi,

Really interested in this project and have a donation in for a manual. But I'm wed to klipper for this printer. I have seen the faq and previously raised topics on this but have not seen this particular idea addressed.

I was wondering if using klippers customisable macros could help integration, e. g.

setting up tool change macros on klipper, which sent text over serial (via shell commands) to the smuff control board as per octoprint plugin.

What i don't know is how complicated that would get, e.g. how many macros, how much 2 way comms, error handling etc, but my thinking is that should be encapsulated in the octoprint project? Possibly extracted into a generic serial interface project?

I saw your comment that other tool change systems are available for klipper, and have been thinking of a 5 extruder, multi line switching / filament shaping solution, but much prefer the smuff if i can make it work - any other suggestions very welcome.

Thanks!

technik-gegg, 2022-03-02:
Mind you discussing this topic over on Discord, since it's not really an issue of the SMuFF firmware but rather a feature in Klipper?

Closed 2022-03-02.

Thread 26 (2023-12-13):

Firmware Compile for Artillery Ruby board

JoJos1220, 2023-12-13:
Hi,

i have a question regarding the build of the Firmware. In the past I have changed an Artillery Ruby board of my Sidewinder X2 because of an Hotend Issue. I have found out that the Thiristor is blown up....actually a trivial thing - i can change it and it run OK until i saw this project:
Currently I am thinking about building a SMUFF for myself and i want to use this Artillery Ruby Mainboard instead of the SKR mini board because it would actually fit perfectly and the Thermistor Output for the Hotend Heating is not needed for it.
Is it possible to build the Firmware for the Artillery Ruby board? Have someone experience with it?

technik-gegg, 2023-12-13:
Please join us on [Discord](https://discord.com/invite/BzZ3rBf) for such questions.

Closed 2023-12-13.

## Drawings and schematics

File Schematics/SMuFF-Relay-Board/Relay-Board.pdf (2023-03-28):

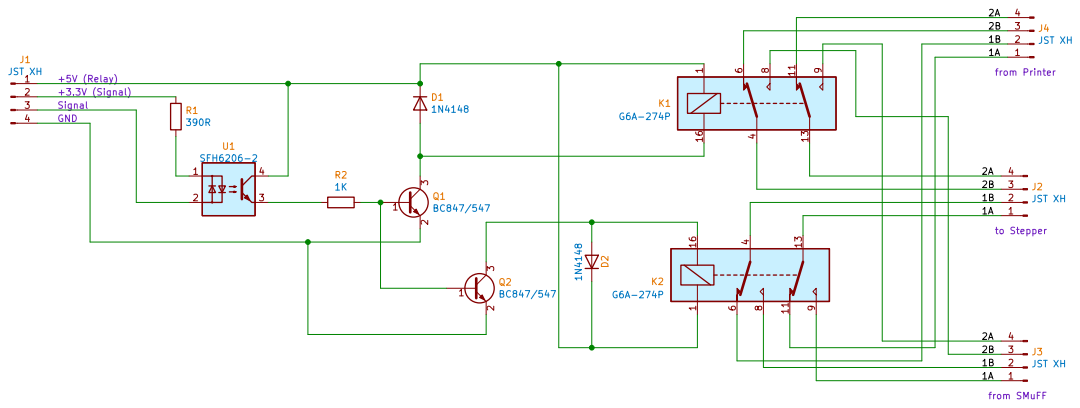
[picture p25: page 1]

AISLER Project ID: FMWPPUGV

File: Relay-Board.kicad_sch Sheet: / Technik Gegg

Id: 1/1 Title: SMuFF Mini Relay Board

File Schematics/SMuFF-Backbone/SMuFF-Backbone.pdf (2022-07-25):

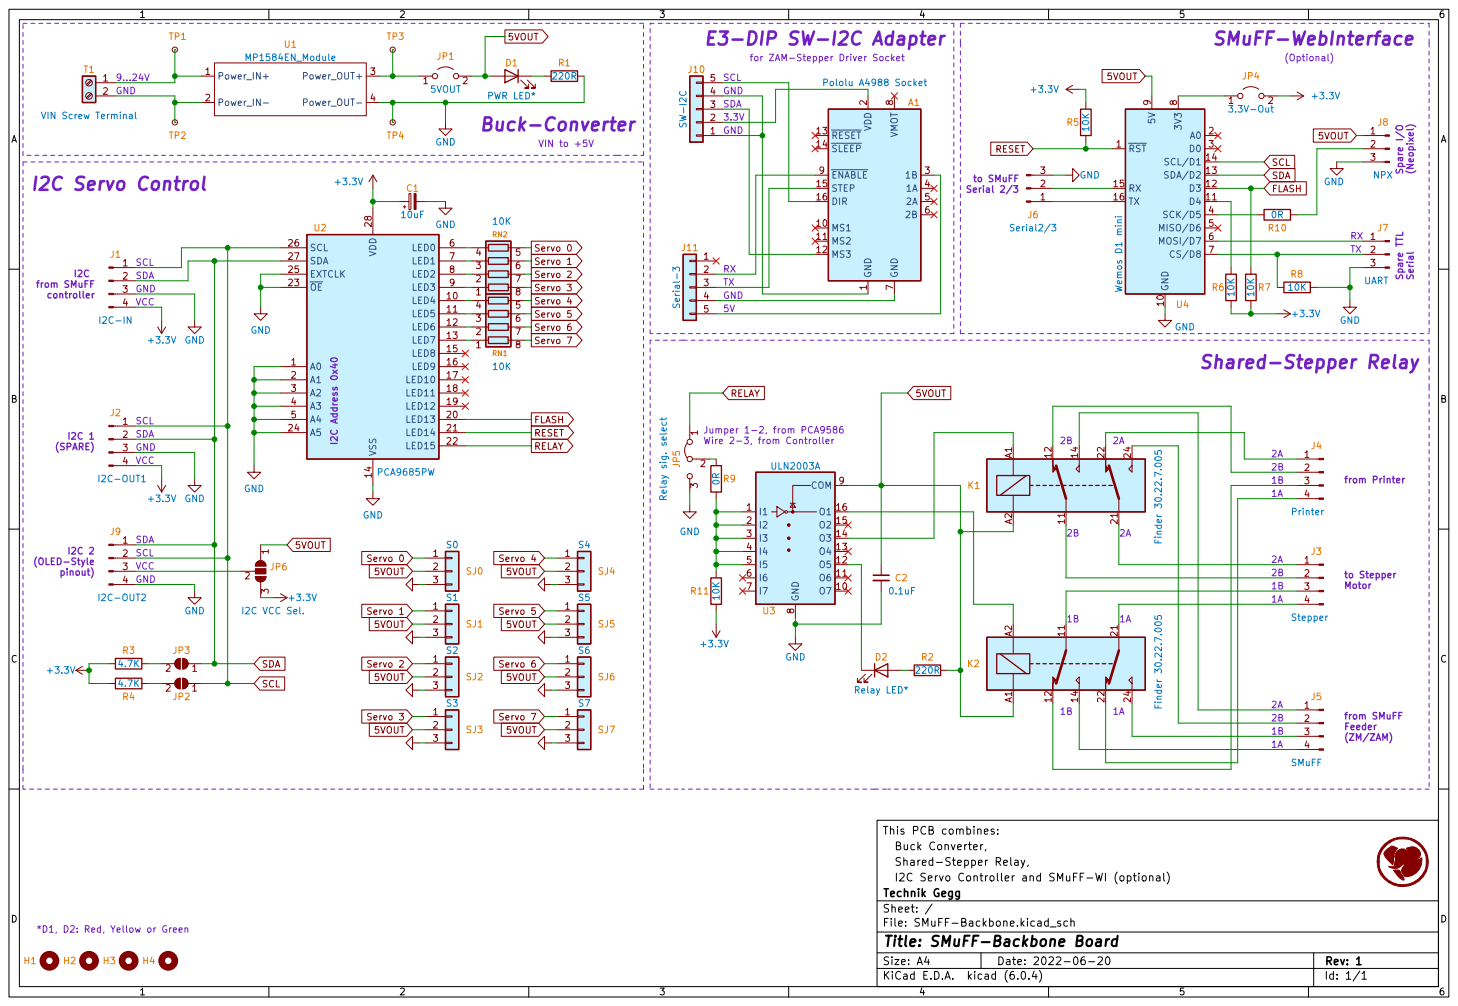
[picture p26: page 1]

for ZAM-Stepper Driver Socket SDA GND
1B GND

VIN to +5V Buck-Converter

1 MS1 10 MS2 11 MS3 12 ~{RESET} 13 ~{SLEEP} 14 STEP 15 DIR 16 VDD

Jumper 1-2, from PCA9586 Wire 2-3, from Controller
D2 Relay LED* 1 2

1B 3
1A 4

Buck Converter, This PCB combines:

Shared-Stepper Relay,
I2C Servo Controller and SMuFF-WI (optional)
File: SMuFF-Backbone.kicad_sch Sheet: / Technik Gegg

*D1, D2: Red, Yellow or Green

Id: 1/1 Title: SMuFF-Backbone Board

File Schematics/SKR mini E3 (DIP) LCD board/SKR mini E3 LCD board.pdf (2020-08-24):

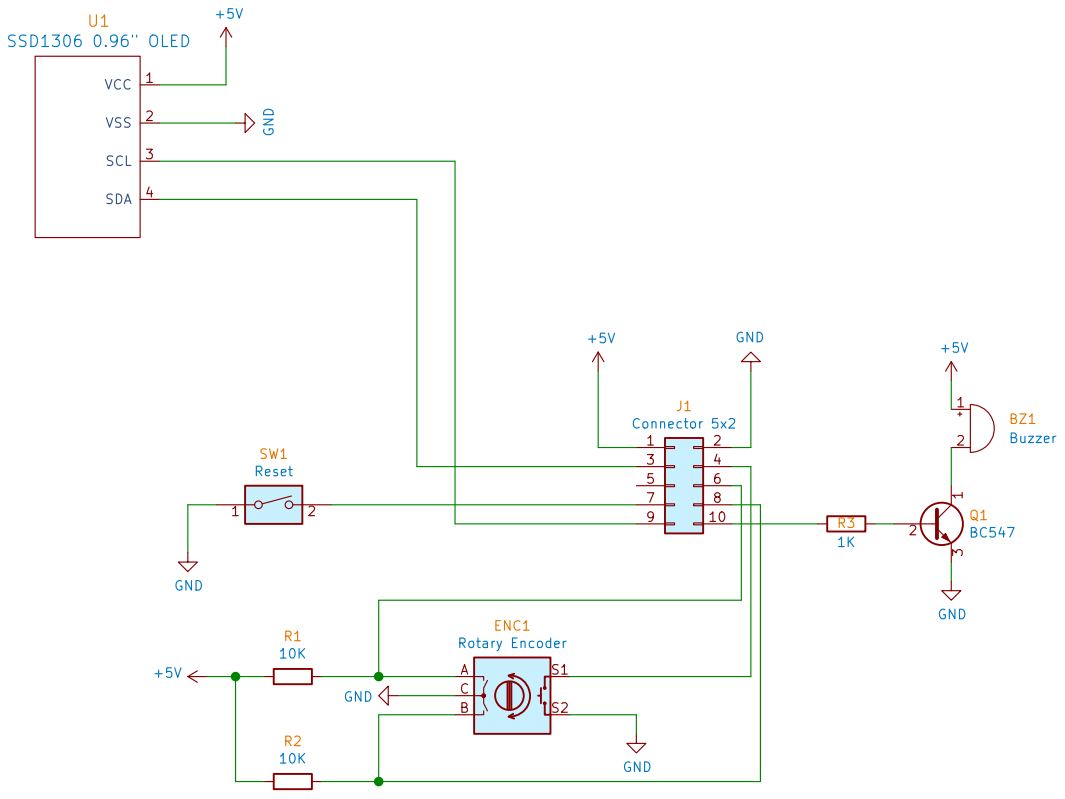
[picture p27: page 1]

File: SKR mini E3 LCD board.sch Sheet: / Technik Gegg

Id: 1/1 Title: SKR Mini E3 (DIP) LCD board

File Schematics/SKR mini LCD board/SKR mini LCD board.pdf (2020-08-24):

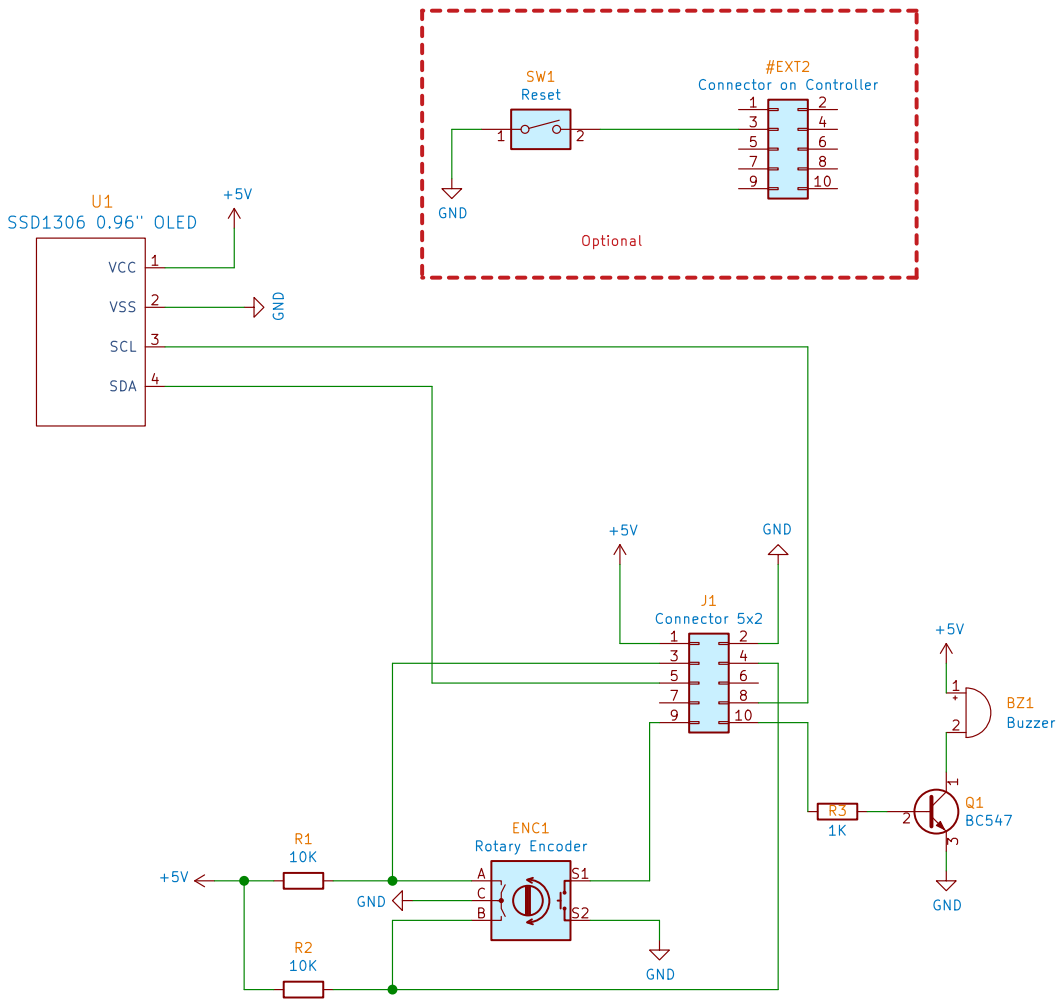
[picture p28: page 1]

File: SKR mini LCD board.sch Sheet: / Technik Gegg

Id: 1/1 Title: SKR Mini V1.1 LCD board

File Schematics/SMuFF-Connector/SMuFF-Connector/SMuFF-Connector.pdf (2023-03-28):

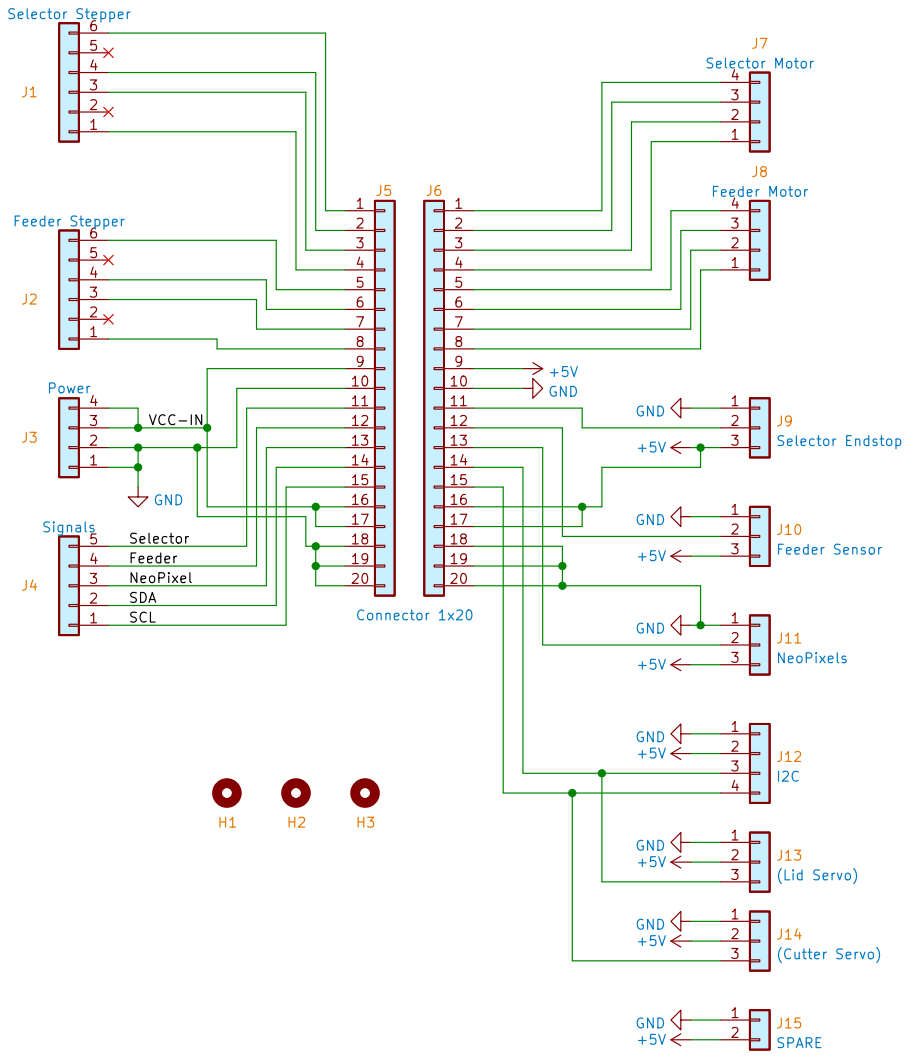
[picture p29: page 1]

Id: 1/1 Title: SMuFF Connector Board

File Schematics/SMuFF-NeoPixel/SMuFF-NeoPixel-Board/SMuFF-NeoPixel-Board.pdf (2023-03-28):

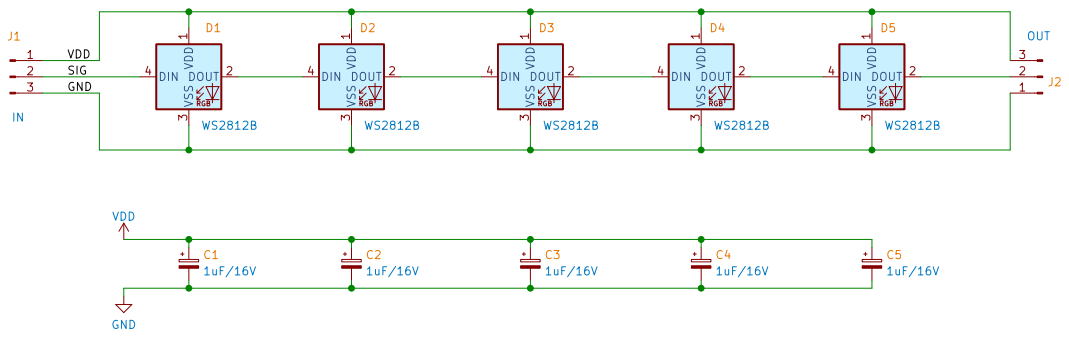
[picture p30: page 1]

File: SMuFF NeoPixel Board.kicad_sch Sheet: / Technik gegg C3

Id: 1/1 Title: SMuFF Tools NeoPixel Board

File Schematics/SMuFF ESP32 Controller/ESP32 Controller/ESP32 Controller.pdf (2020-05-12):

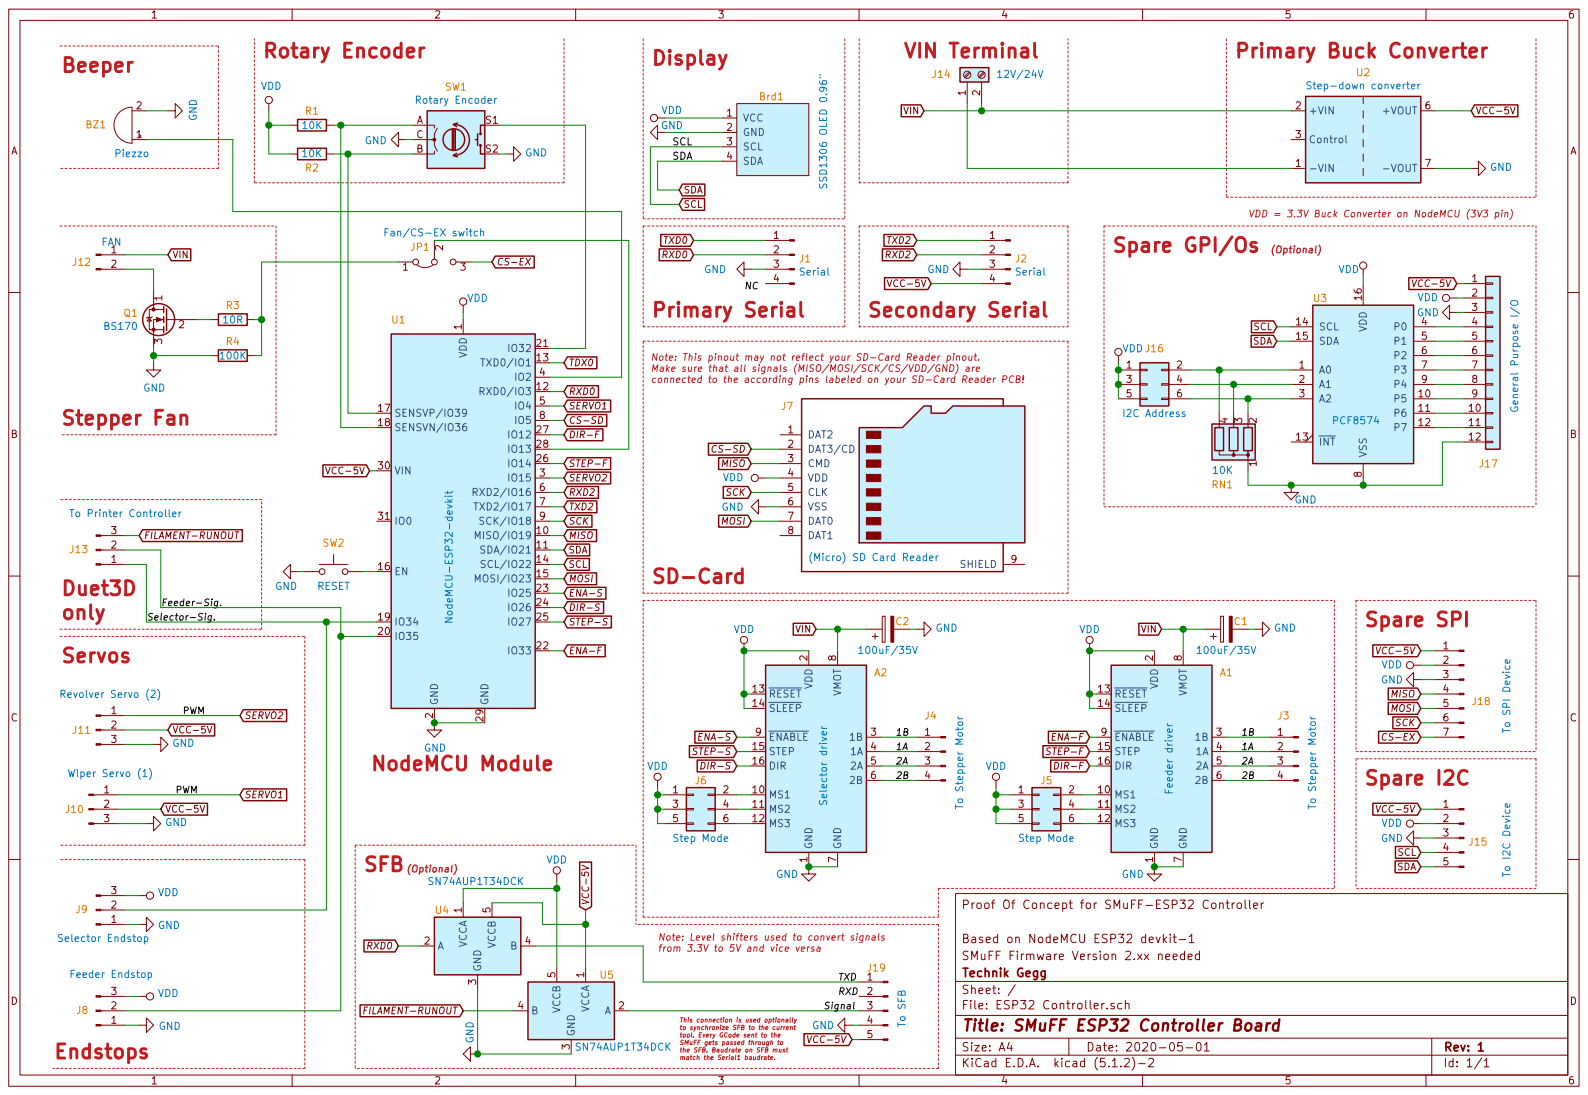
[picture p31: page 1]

CS-EX Spare SPI SDA

1 MISO/IO19 10 SDA/IO21 11 RXD0/IO3 12 TXD0/IO1 13 SCL/IO22 14 MOSI/IO23 EN 15

connected to the according pins labeled on your SD-Card Reader PCB! 1B

(Micro) SD Card Reader GND

SCL SDA MOSI MISO

VCC-5V
J18 To SPI DeviceVDD GND

8 ENABLE 9 A1 Feeder driver GND

1 MS1 10 MS2 11 MS3 12 RESET 13 SLEEP 14 STEP 15 DIR 16 VDD

File: ESP32 Controller.sch Sheet: / Technik Gegg SMuFF Firmware Version 2.xx needed Based on NodeMCU ESP32 devkit-1 Proof Of Concept for SMuFF-ESP32 Controller GND

J9 Selector Endstop
J8 Feeder Endstop VDD GND

Note: Level shifters used to convert signals

Id: 1/1 Title: SMuFF ESP32 Controller Board

This connection is used optionally
to synchronize SFB to the current
tool. Every GCode sent to the SMuFF gets passed through to

the SFB. Baudrate on SFB must match the Serial1 baudrate.

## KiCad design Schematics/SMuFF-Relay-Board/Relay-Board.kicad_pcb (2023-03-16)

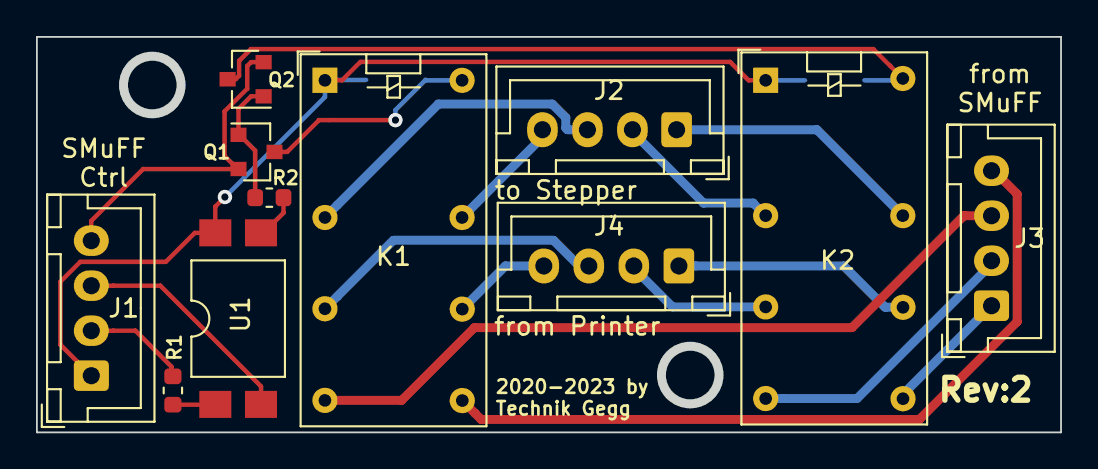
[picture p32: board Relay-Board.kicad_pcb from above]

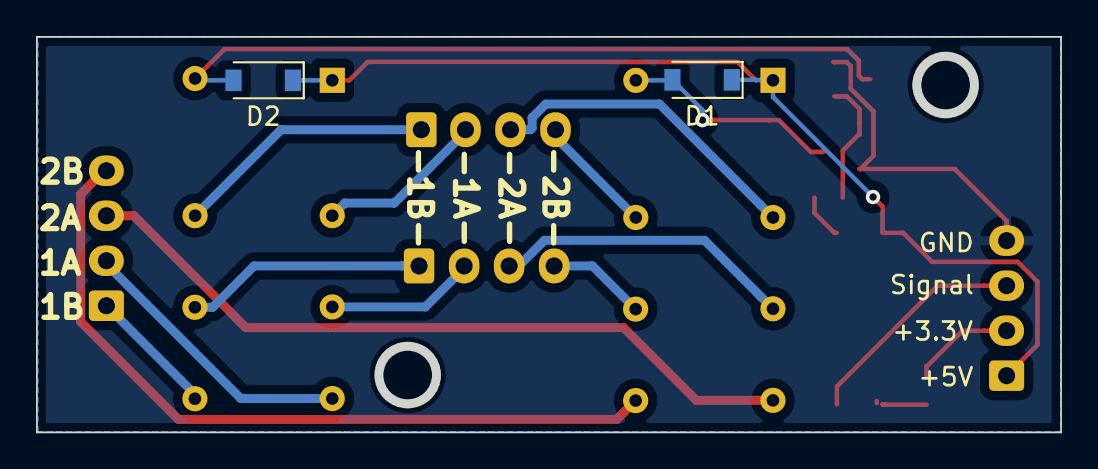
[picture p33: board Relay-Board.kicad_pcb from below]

Board: 2 copper layers, 56.9 x 22.0 mm, 13 parts (2 on the bottom side), 21 nets.

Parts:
D1, D2: 1N4148; D_SOD-123
J1, J2, J3, J4: JST XH; JST_XH_B4B-XH-A_1x04_P2.50mm_Vertical
K1, K2: G6A-274P; Relay_DPDT_Omron_G5V-2
Q1, Q2: BC847/547; SOT-23
R1: 390R; R_0603_1608Metric
R2: 1K; R_0603_1608Metric
U1: TLP521; SMDIP-4_W9.53mm_Clearance8mm

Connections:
unnamed: D1.1, D2.1, J1.1, K1.1, K2.1, U1.4
unnamed: D1.2, K1.16, Q1.3
unnamed: D2.2, K2.16, Q2.3
unnamed: J1.2, R1.1
unnamed: J1.3, U1.2
unnamed: J1.4, Q1.2, Q2.2
unnamed: J2.1, K2.13
unnamed: J2.2, K2.4
unnamed: J2.3, K1.4
unnamed: J2.4, K1.13
unnamed: J3.1, K2.9
unnamed: J3.2, K2.8
unnamed: J3.3, K1.8
unnamed: J3.4, K1.9
unnamed: J4.1, K2.11
unnamed: J4.2, K2.6
unnamed: J4.3, K1.6
unnamed: J4.4, K1.11
unnamed: Q1.1, Q2.1, R2.1
unnamed: R1.2, U1.1
unnamed: R2.2, U1.3

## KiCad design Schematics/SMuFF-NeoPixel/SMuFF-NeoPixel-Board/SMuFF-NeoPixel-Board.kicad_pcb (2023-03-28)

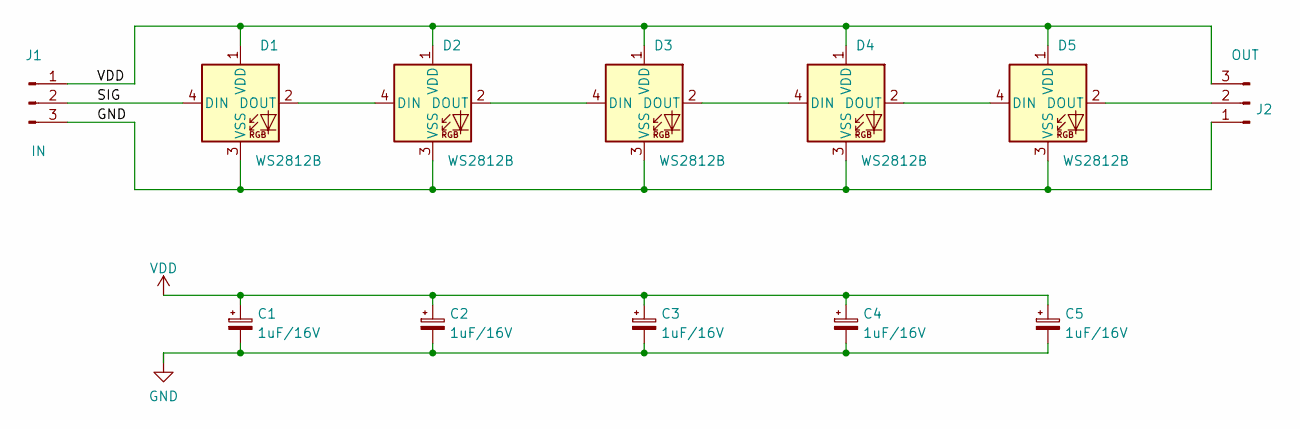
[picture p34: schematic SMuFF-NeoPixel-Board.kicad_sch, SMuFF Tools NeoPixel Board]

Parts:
C1, C2, C3, C4, C5: 1uF/16V; CP_EIA-2012-12_Kemet-R
D1, D2, D3, D4, D5: WS2812B; LED_WS2812B_PLCC4_5.0x5.0mm_P3.2mm
J1: IN; PinHeader_1x03_P2.54mm_Vertical_SMD_NeoPixel
J2: OUT; PinHeader_1x03_P2.54mm_Vertical_SMD_NeoPixel

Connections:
/SIG: D1.4 (DIN), J1.2
GND: C1.2, C2.2, C3.2, C4.2, C5.2, D1.3 (VSS), D2.3 (VSS), D3.3 (VSS), D4.3 (VSS), D5.3 (VSS), J1.3, J2.1
unnamed: D1.2 (DOUT), D2.4 (DIN)
unnamed: D2.2 (DOUT), D3.4 (DIN)
unnamed: D3.2 (DOUT), D4.4 (DIN)
unnamed: D4.2 (DOUT), D5.4 (DIN)
unnamed: D5.2 (DOUT), J2.2
VDD: C1.1, C2.1, C3.1, C4.1, C5.1, D1.1 (VDD), D2.1 (VDD), D3.1 (VDD), D4.1 (VDD), D5.1 (VDD), J1.1, J2.3

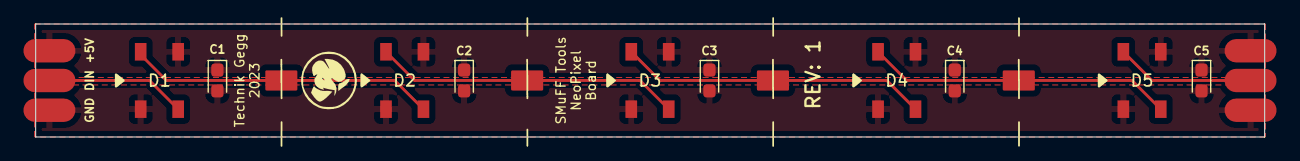
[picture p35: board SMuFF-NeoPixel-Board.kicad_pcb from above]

Board: 2 copper layers, 105.0 x 9.7 mm, 12 parts (0 on the bottom side), 8 nets.

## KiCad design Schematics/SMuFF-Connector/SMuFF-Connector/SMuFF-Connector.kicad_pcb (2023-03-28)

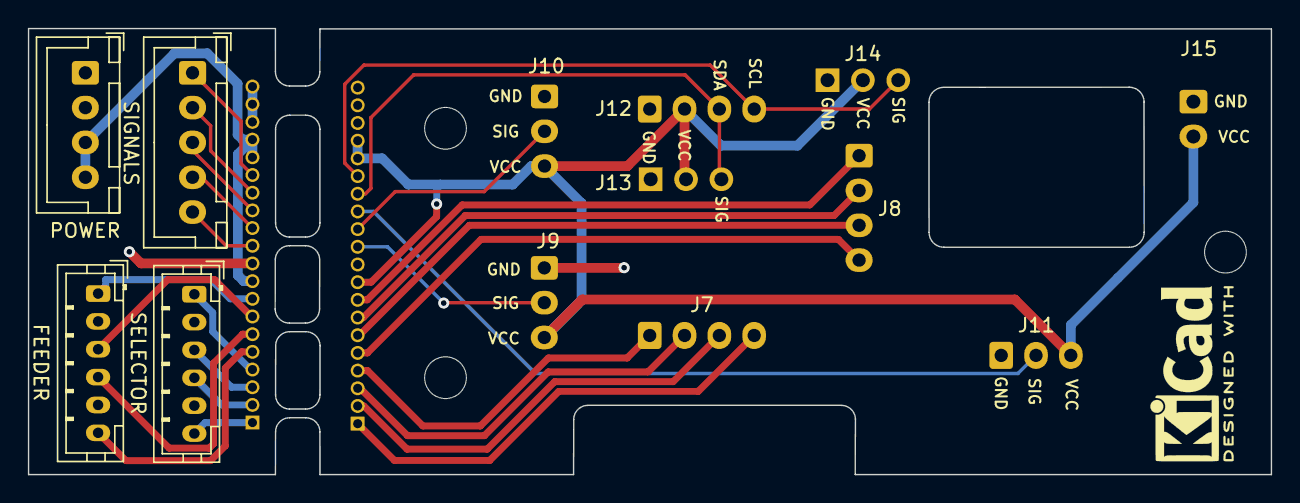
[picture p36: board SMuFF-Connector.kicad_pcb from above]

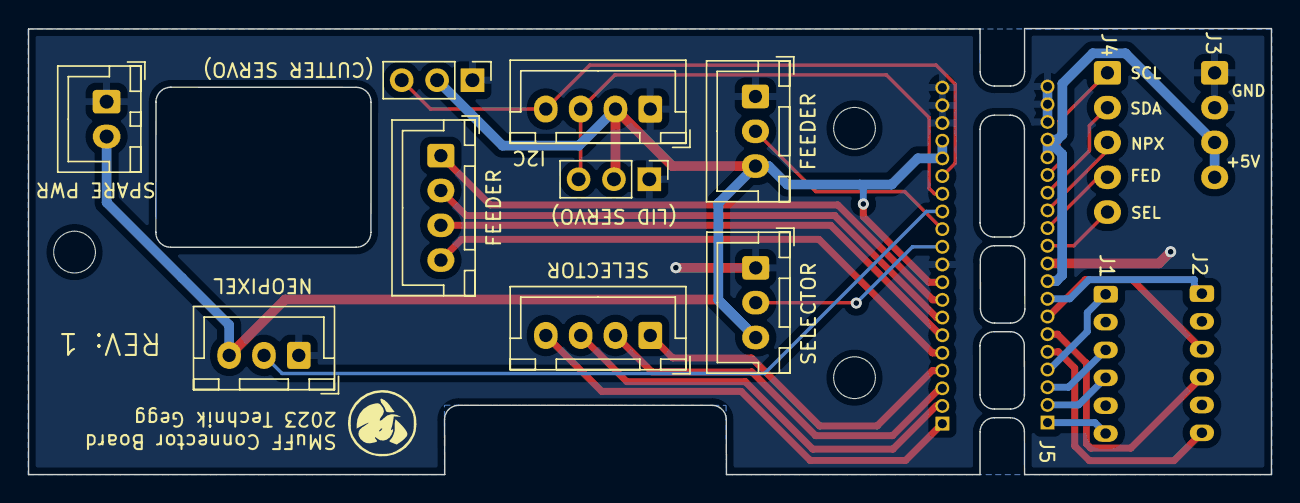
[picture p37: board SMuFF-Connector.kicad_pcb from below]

Board: 2 copper layers, 89.2 x 32.0 mm, 18 parts (11 on the bottom side), 29 nets.

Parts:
H1, H2, H3: MountingHole; MountingHole_3mm
J1: Selector Stepper; JST_PH_B6B-PH-K_1x06_P2.00mm_Vertical
J2: Feeder Stepper; JST_PH_B6B-PH-K_1x06_P2.00mm_Vertical
J3: Power; JST_XH_B4B-XH-A_1x04_P2.50mm_Vertical
J4: Signals; JST_XH_B5B-XH-A_1x05_P2.50mm_Vertical
J5: Connector 1x20; PinHeader_1x20_P1.27mm_Horizontal
J6: Conn_01x16; PinHeader_1x20_P1.27mm_Vertical
J7: Selector Motor; JST_XH_B4B-XH-A_1x04_P2.50mm_Vertical
J8: Feeder Motor; JST_XH_B4B-XH-A_1x04_P2.50mm_Vertical
J9: Selector Endstop; JST_XH_B3B-XH-A_1x03_P2.50mm_Vertical
J10: Feeder Sensor; JST_XH_B3B-XH-A_1x03_P2.50mm_Vertical
J11: NeoPixels; JST_XH_B3B-XH-A_1x03_P2.50mm_Vertical
J12: I2C; JST_XH_B4B-XH-A_1x04_P2.50mm_Vertical
J13: (Lid Servo); PinHeader_1x03_P2.54mm_Vertical
J14: (Cutter Servo); PinHeader_1x03_P2.54mm_Vertical
J15: SPARE; JST_XH_B2B-XH-A_1x02_P2.50mm_Vertical

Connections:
+5V: J6.9, J6.16, J6.17, J9.3, J10.3, J11.3, J12.2, J13.2, J14.2, J15.2
/Feeder: J4.4, J5.12
/NeoPixel: J4.3, J5.13
/SCL: J4.1, J5.15
/SDA: J4.2, J5.14
/Selector: J4.5, J5.11
/VCC-IN: J3.3, J3.4, J5.9, J5.16, J5.17
GND: J3.1, J3.2, J5.10, J5.18, J5.19, J5.20, J6.10, J6.18, J6.19, J6.20, J9.1, J10.1, J11.1, J12.1, J13.1, J14.1, J15.1
unnamed: J1.1, J5.4
unnamed: J1.3, J5.3
unnamed: J1.4, J5.2
unnamed: J1.6, J5.1
unnamed: J2.1, J5.8
unnamed: J2.3, J5.7
unnamed: J2.4, J5.6
unnamed: J2.6, J5.5
unnamed: J6.1, J7.4
unnamed: J6.2, J7.3
unnamed: J6.3, J7.2
unnamed: J6.4, J7.1
unnamed: J6.5, J8.4
unnamed: J6.6, J8.3
unnamed: J6.7, J8.2
unnamed: J6.8, J8.1
unnamed: J6.11, J9.2
unnamed: J6.13, J11.2
unnamed: J6.12, J10.2
unnamed: J6.14, J12.3, J13.3
unnamed: J6.15, J12.4, J14.3

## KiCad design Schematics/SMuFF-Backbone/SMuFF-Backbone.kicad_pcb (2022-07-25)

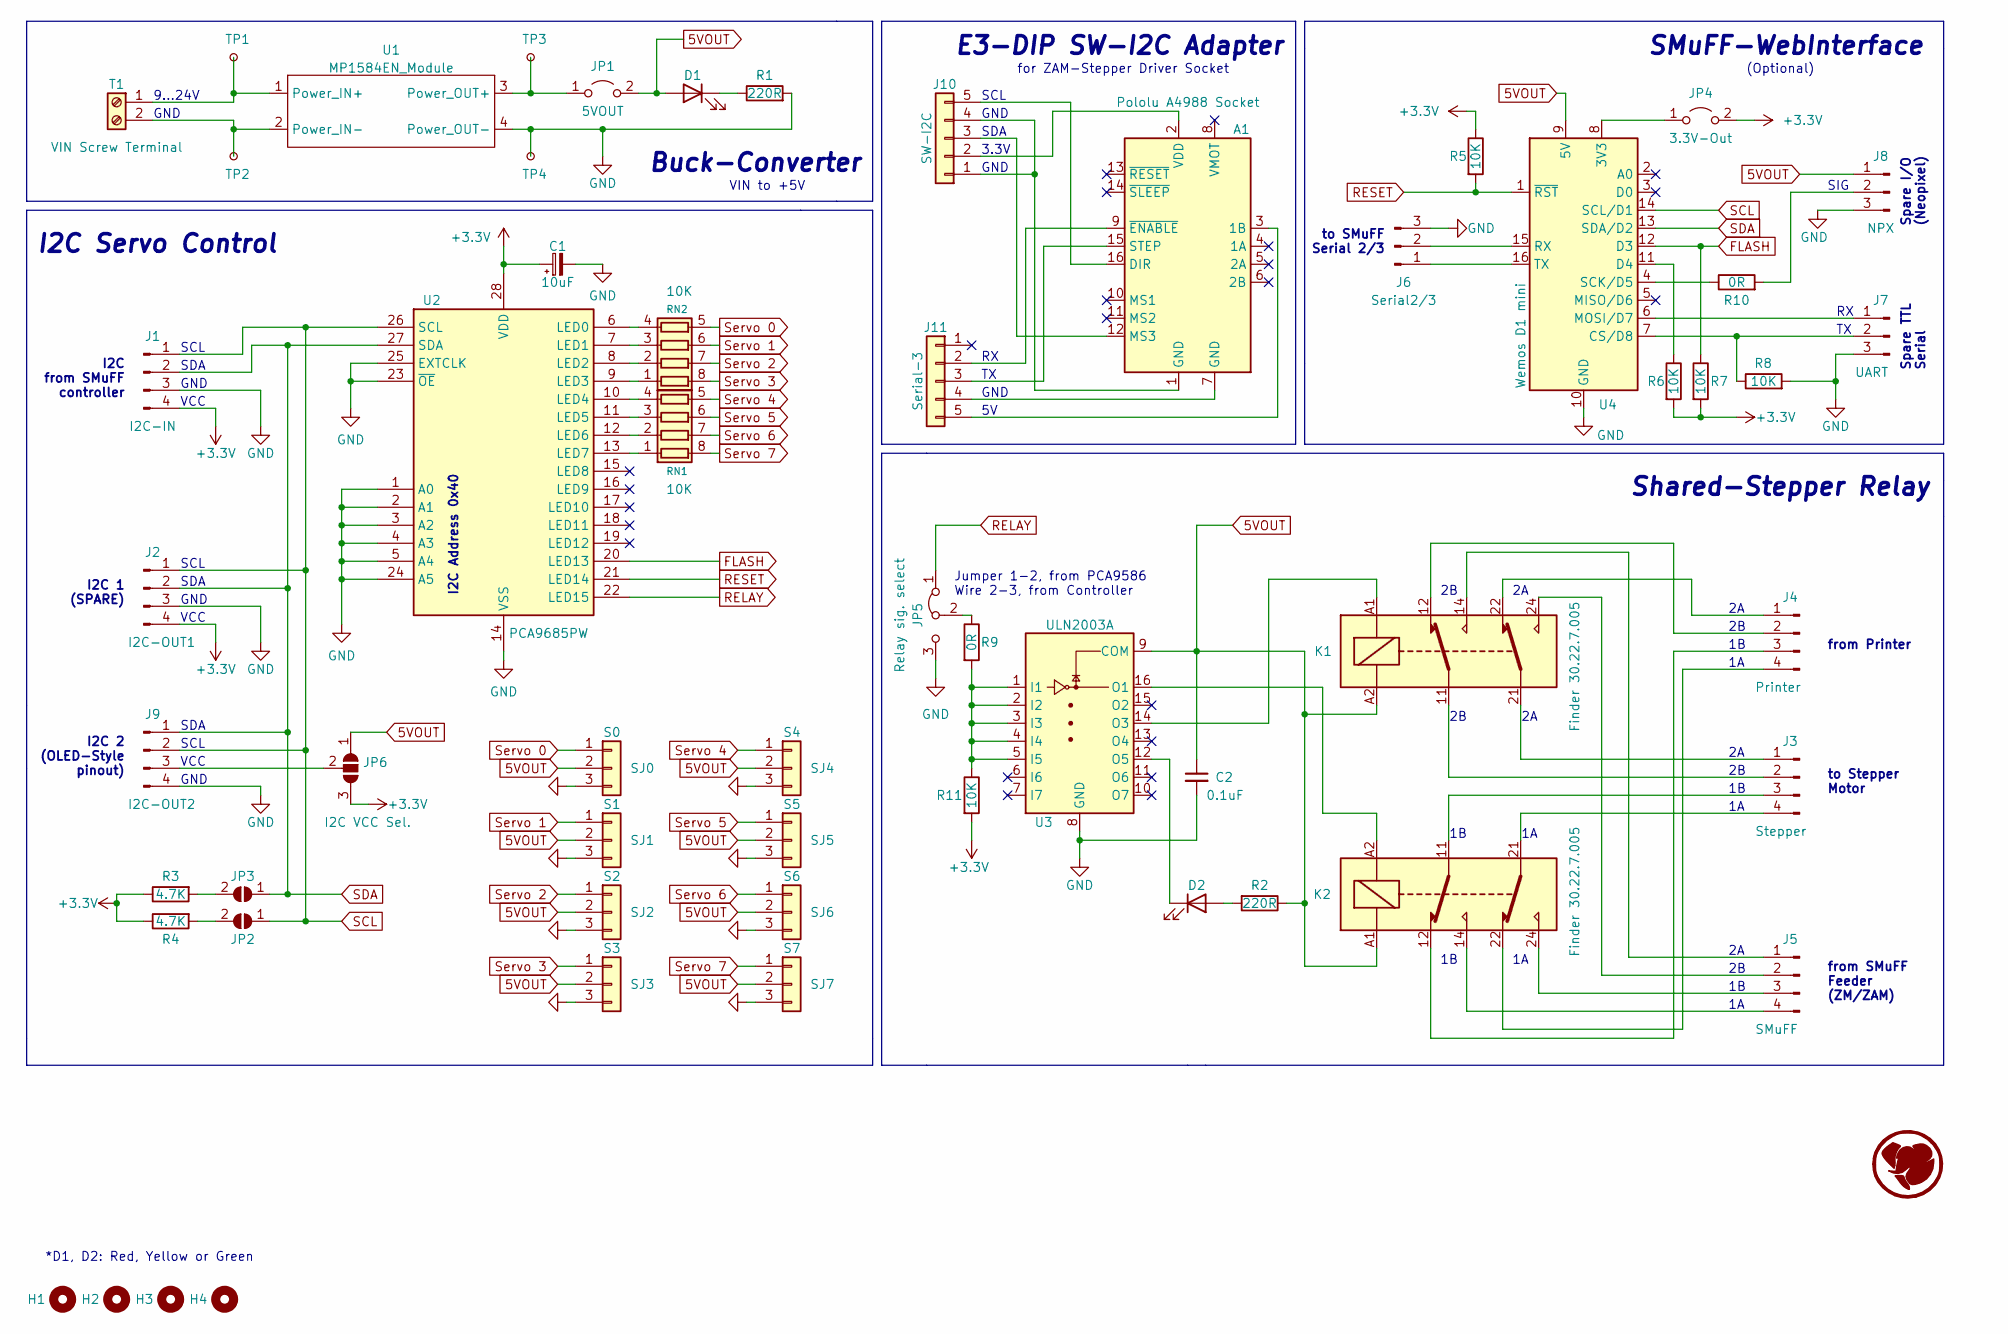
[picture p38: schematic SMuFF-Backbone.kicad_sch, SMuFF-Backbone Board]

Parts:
A1: Pololu A4988 Socket; C_1206_3216Metric
C1: 10uF; C_1206_3216Metric
C2: 0.1uF; C_1206_3216Metric
D1, D2: (no value)
H1, H2, H3, H4: MountingHole; MountingHole_3.2mm_M3
J1: I2C-IN; JST_XH_B4B-XH-A_1x04_P2.50mm_Vertical
J2: I2C-OUT1; PinHeader_1x04_P2.54mm_Vertical
J3: Stepper; JST_XH_B4B-XH-A_1x04_P2.50mm_Vertical
J4: Printer; JST_XH_B4B-XH-A_1x04_P2.50mm_Vertical
J5: SMuFF; JST_XH_B4B-XH-A_1x04_P2.50mm_Vertical
J6: Serial2/3; JST_XH_B3B-XH-A_1x03_P2.50mm_Vertical
J7: UART; JST_XH_B3B-XH-A_1x03_P2.50mm_Vertical
J8: NPX; JST_XH_B3B-XH-A_1x03_P2.50mm_Vertical
J9: I2C-OUT2; PinHeader_1x04_P2.54mm_Vertical
J10: SW-I2C; JST_XH_B5B-XH-A_1x05_P2.50mm_Vertical
J11: Serial-3; PinHeader_1x05_P2.54mm_Vertical
JP1: 5VOUT; PinHeader_1x02_P2.54mm_Vertical
JP2, JP3: Jumper; SolderJumper-2_P1.3mm_Open_RoundedPad1.0x1.5mm
JP4: 3.3V-Out; PinHeader_1x02_P2.54mm_Vertical
JP5: Relay sig. select; PinHeader_1x03_P2.54mm_Vertical
JP6: I2C VCC Sel.; SolderJumper-3_P1.3mm_Open_RoundedPad1.0x1.5mm
K1, K2: Finder 30.22.7.005; Relay_DPDT_Finder_30.22
R1, R2: 220R; R_0805_2012Metric
R3, R4: 4.7K; R_0805_2012Metric
R5, R6, R7, R8, R11: 10K; R_0805_2012Metric
R9, R10: 0R; R_0805_2012Metric
RN1, RN2: 10K; R_Array_Concave_4x0603
SJ0: S0; PinHeader_1x03_P2.54mm_Vertical
SJ1: S1; PinHeader_1x03_P2.54mm_Vertical
SJ2: S2; PinHeader_1x03_P2.54mm_Vertical
SJ3: S3; PinHeader_1x03_P2.54mm_Vertical
SJ4: S4; PinHeader_1x03_P2.54mm_Vertical
SJ5: S5; PinHeader_1x03_P2.54mm_Vertical
SJ6: S6; PinHeader_1x03_P2.54mm_Vertical
SJ7: S7; PinHeader_1x03_P2.54mm_Vertical
T1: VIN Screw Terminal; TerminalBlock_bornier-2_P5.08mm
TP1: SY8205-IN+; TestPoint_THTPad_1.5x1.5mm_Drill0.7mm
TP2: SY8205-IN-; TestPoint_THTPad_1.5x1.5mm_Drill0.7mm
TP3: SY8205-OUT+; TestPoint_THTPad_1.5x1.5mm_Drill0.7mm
TP4: SY8205-OUT-; TestPoint_THTPad_1.5x1.5mm_Drill0.7mm
U1: MP1584EN_Module
U2: PCA9685PW; TSSOP-28_4.4x9.7mm_P0.65mm
U3: ULN2003A; SOIC-16_3.9x9.9mm_P1.27mm
U4: Wemos D1 mini; WEMOS_D1_mini_light

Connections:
5VOUT: C2.1, D1.2 (A), J8.1, JP1.2 (B), JP6.1 (A), K1.A2, K2.A1, R2.1, SJ0.2, SJ1.2, SJ2.2, SJ3.2, SJ4.2, SJ5.2, SJ6.2, SJ7.2, U3.9 (COM), U4.9 (5V)
+3V3: C1.1, J1.4, J2.4, JP4.2 (B), JP6.3 (B), R3.1, R4.1, R5.1, R6.2, R7.2, R11.2, U2.28 (VDD)
FLASH: R7.1, U2.20 (LED13), U4.12 (D3)
GND: C1.2, C2.2, J1.3, J2.3, J6.3, J7.3, J8.3, J9.4, JP5.3 (B), R1.2, R8.2, SJ0.3, SJ1.3, SJ2.3, SJ3.3, SJ4.3, SJ5.3, SJ6.3, SJ7.3, TP4.1, U1.4 (Power_OUT-), U2.1 (A0), U2.2 (A1), U2.3 (A2), U2.4 (A3), U2.5 (A4), U2.14 (VSS), U2.23 (~OE), U2.24 (A5), U2.25 (EXTCLK), U3.8 (GND), U4.10 (GND)
unnamed: A1.1 (GND), J10.1, J10.4
unnamed: A1.2 (VDD), J10.2
unnamed: A1.3 (1B), J11.5
unnamed: A1.7 (GND), J11.4
unnamed: A1.9 (~ENABLE), J11.2
unnamed: A1.12 (MS3), J10.3
unnamed: A1.15 (STEP), J11.3
unnamed: A1.16 (DIR), J10.5
unnamed: D1.1 (K), R1.1
unnamed: D2.1 (K), U3.12 (O5)
unnamed: D2.2 (A), R2.2
unnamed: J3.1, K1.21
unnamed: J3.2, K1.11
unnamed: J3.3, K2.11
unnamed: J3.4, K2.21
unnamed: J4.1, K1.22
unnamed: J4.2, K1.12
unnamed: J4.3, K2.12
unnamed: J4.4, K2.22
unnamed: J5.1, K1.14
unnamed: J5.2, K1.24
unnamed: J5.3, K2.24
unnamed: J5.4, K2.14
unnamed: J6.1, U4.16 (TX)
unnamed: J6.2, U4.15 (RX)
unnamed: J7.1, U4.6 (MOSI/D7)
unnamed: J7.2, R8.1, U4.7 (CS/D8)
unnamed: J8.2, R10.2
unnamed: J9.3, JP6.2 (C)
unnamed: JP1.1 (A), TP3.1, U1.3 (Power_OUT+)
unnamed: JP2.2 (B), R4.2
unnamed: JP3.2 (B), R3.2
unnamed: JP4.1 (A), U4.8 (3V3)
unnamed: JP5.2 (C), R9.1
unnamed: K1.A1, U3.14 (O3)
unnamed: K2.A2, U3.16 (O1)
unnamed: R6.1, U4.11 (D4)
unnamed: R10.1, U4.4 (SCK/D5)
unnamed: R9.2, R11.1, U3.1 (I1), U3.2 (I2), U3.3 (I3), U3.4 (I4), U3.5 (I5)
unnamed: RN1.1 (R1.1), U2.9 (LED3)
unnamed: RN1.2 (R2.1), U2.8 (LED2)
unnamed: RN1.3 (R3.1), U2.7 (LED1)
unnamed: RN1.4 (R4.1), U2.6 (LED0)
unnamed: RN2.1 (R1.1), U2.13 (LED7)
unnamed: RN2.2 (R2.1), U2.12 (LED6)
unnamed: RN2.3 (R3.1), U2.11 (LED5)
unnamed: RN2.4 (R4.1), U2.10 (LED4)
unnamed: T1.1, TP1.1, U1.1 (Power_IN+)
unnamed: T1.2, TP2.1, U1.2 (Power_IN-)
RELAY: JP5.1 (A), U2.22 (LED15)
RESET: R5.2, U2.21 (LED14), U4.1 (~RST)
SCL: J1.1, J2.1, J9.2, JP2.1 (A), U2.26 (SCL), U4.14 (SCL/D1)
SDA: J1.2, J2.2, J9.1, JP3.1 (A), U2.27 (SDA), U4.13 (SDA/D2)
Servo 0: RN1.5 (R4.2), SJ0.1
Servo 1: RN1.6 (R3.2), SJ1.1
Servo 2: RN1.7 (R2.2), SJ2.1
Servo 3: RN1.8 (R1.2), SJ3.1
Servo 4: RN2.5 (R4.2), SJ4.1
Servo 5: RN2.6 (R3.2), SJ5.1
Servo 6: RN2.7 (R2.2), SJ6.1
Servo 7: RN2.8 (R1.2), SJ7.1

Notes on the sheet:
SCL
GND
I2C 2 (OLED-Style pinout)
9...24V
I2C from SMuFF controller
Buck-Converter
I2C 1 (SPARE)
Jumper 1-2, from PCA9586 Wire 2-3, from Controller
to Stepper Motor
to SMuFF Serial 2/3
VIN to +5V
I2C Address 0x40
(Optional)
for ZAM-Stepper Driver Socket
from SMuFF Feeder (ZM/ZAM)
SMuFF-WebInterface
Spare TTL Serial
*D1, D2: Red, Yellow or Green
SDA
SIG
VCC
Spare I/O (Neopixel)
3.3V
E3-DIP SW-I2C Adapter
Shared-Stepper Relay
I2C Servo Control
from Printer

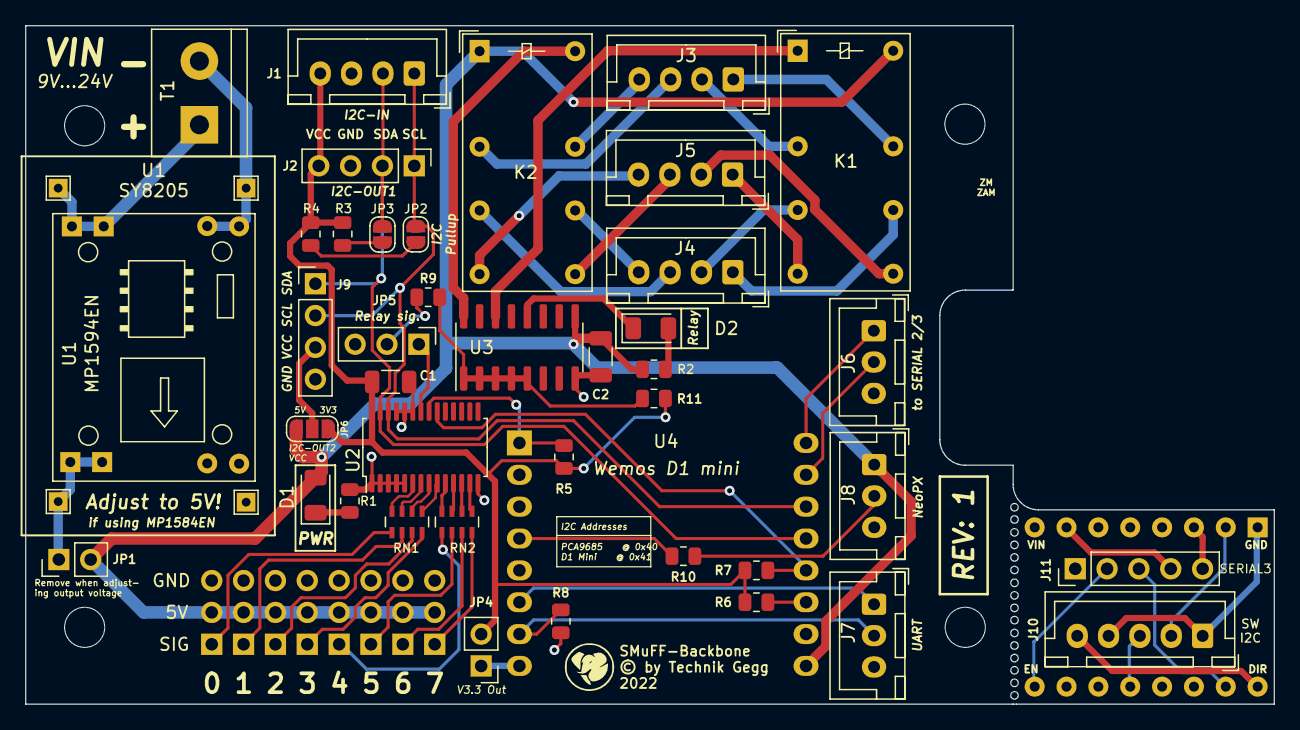
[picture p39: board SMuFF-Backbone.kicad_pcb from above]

Board: 2 copper layers, 99.6 x 54.1 mm, 58 parts (0 on the bottom side), 65 nets.

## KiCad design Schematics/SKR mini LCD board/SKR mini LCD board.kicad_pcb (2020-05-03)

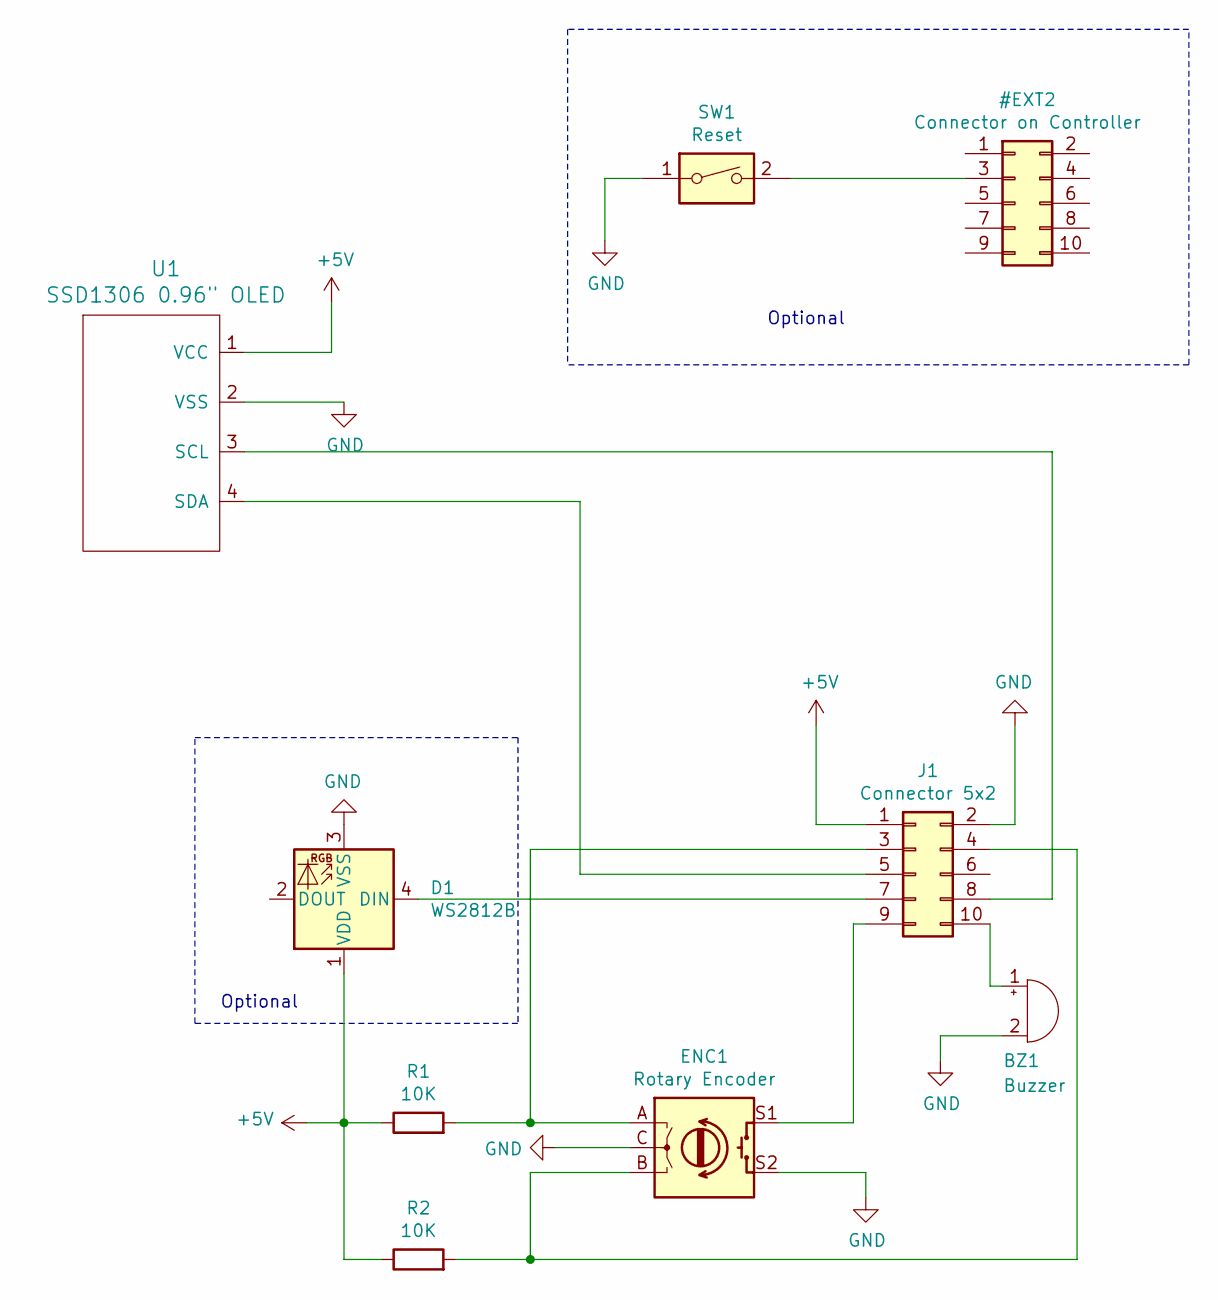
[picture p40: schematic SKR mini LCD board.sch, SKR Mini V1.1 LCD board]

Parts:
BZ1: Buzzer; Buzzer_12x9.5RM7.6
D1: WS2812B; LED_WS2812B_PLCC4_5.0x5.0mm_P3.2mm
ENC1: Rotary Encoder; RotaryEncoder_Alps_EC11E-Switch_Vertical_H20mm_CircularMoun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
J1: Connector 5x2; PinSocket_2x05_P2.54mm_Vertical
R1, R2: 10K; R_Axial_DIN0207_L6.3mm_D2.5mm_P10.16mm_Horizontal
SW1: Reset; SW_PUSH_6mm_H7.3mm
U1: SSD1306 0.96\" OLED; PinHeader_1x04_P2.54mm_Vertical

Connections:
+5V: D1.1 (VDD), J1.1, R1.1, R2.1, U1.1 (VCC)
GND: BZ1.2 (+), D1.3 (VSS), ENC1.C, ENC1.S2, J1.2, SW1.1, U1.2 (VSS)
unnamed: BZ1.1 (-), J1.10
unnamed: D1.4 (DIN), J1.7
unnamed: ENC1.A, J1.3, R1.2
unnamed: ENC1.B, J1.4, R2.2
unnamed: ENC1.S1, J1.9
unnamed: J1.5, U1.4 (SDA)
unnamed: J1.8, U1.3 (SCL)

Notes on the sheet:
Optional
Optional

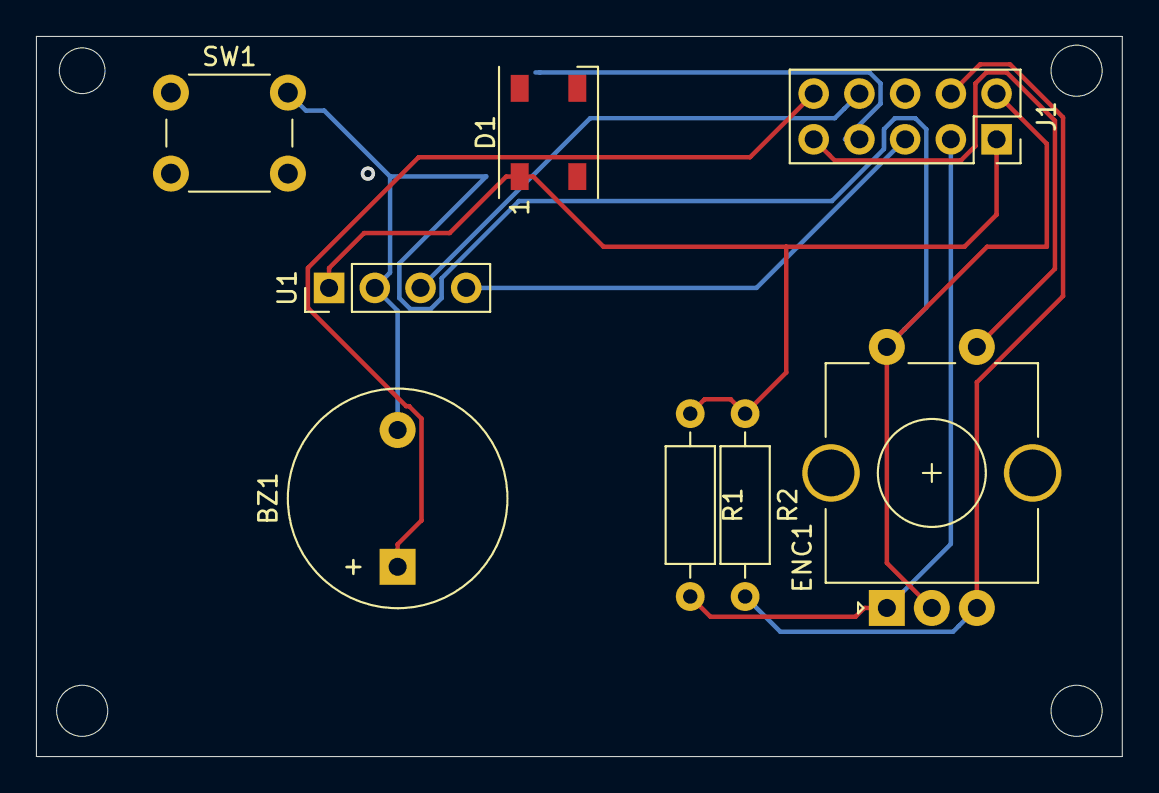
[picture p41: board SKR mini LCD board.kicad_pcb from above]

Board: 2 copper layers, 60.3 x 40.0 mm, 8 parts (0 on the bottom side), 9 nets.

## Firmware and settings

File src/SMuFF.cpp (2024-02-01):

/**
 * SMuFF Firmware
 * Copyright (C) 2019-2024 Technik Gegg
 *
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
 */
#include "SMuFF.h"

#define FASTFLIPDBG       1                               // for firmware debugging only

#if defined(__BRD_SKR_MINI)
Stream                    *debugSerial = &Serial1;        // send debug output to...
Stream                    *terminalSerial = &Serial1;     // send terminal emulation output to ...
#else
Stream                    *debugSerial = &Serial2;        // send debug output to...
Stream                    *terminalSerial = &Serial2;     // send terminal emulation output to ...
#endif
Stream                    *logSerial = &Serial;           // send logs to USB by default

#if defined(USE_SW_SERIAL0)
SoftwareSerial            swSerial0(SW_SERIAL_RX_PIN, SW_SERIAL_TX_PIN, false);  // mainly for testing purpose
#endif

dspDriver                 display = INIT_DSP();           // initialize display driver (see macro in according Display_xxx.h)
ZStepper                  steppers[NUM_STEPPERS];
ZTimer                    stepperTimer;
ZTimer                    gpTimer;
#if defined(USE_FASTLED_TOOLS)
ZTimer                    ledTimer;
#endif
#if defined(USE_ZSERVO) && !defined(USE_MULTISERVO)
ZTimer                    servoTimer;
ZServo                    servoWiper;
ZServo                    servoLid;
ZServo                    servoCutter;
#else
  #if !defined(USE_MULTISERVO)
    Servo                 servoWiper;
    Servo                 servoLid;
    Servo                 servoCutter;
  #endif
#endif
ZFan                      fan;

#if defined(__STM32G0XX)
HardwareSerial            Serial4(RX4_PIN, TX4_PIN);
#endif


#if defined(USE_LEONERD_DISPLAY)
LeoNerdEncoder            encoder(I2C_ENCODER_ADDRESS);
#else
  #if !defined(USE_SERIAL_DISPLAY)
  ClickEncoder            encoder(ENCODER1_PIN, ENCODER2_PIN, ENCODER_BUTTON_PIN, 4);
  #else 
  ClickEncoder            encoder(0, 0, 0, 0);
  #endif
#endif

#if defined(__STM32F1XX) || defined(__STM32F4XX) || defined(__STM32G0XX)
  #if defined(USE_SPLITTER_ENDSTOPS)
  ZEStopMux               splitterMux;
  #endif
#endif

#ifdef HAS_TMC_SUPPORT
TMC2209Stepper            *drivers[NUM_STEPPERS+1];
#endif

#if defined(USE_MULTISERVO)
  #if defined(USE_PCA9685_SW_I2C)
    Adafruit_PWMServoDriver   servoPwm = Adafruit_PWMServoDriver(I2C_SERVOCTL_ADDRESS, I2CBusMS);
  #else
    Adafruit_PWMServoDriver   servoPwm = Adafruit_PWMServoDriver(I2C_SERVOCTL_ADDRESS);
  #endif
int8_t                    servoMapping[16]   = {-1, -1, -1, -1, -1, -1, -1, -1, -1, -1, -1, -1, -1, -1, -1, -1}; // servo output mappings for the Wiper, Lid, Cutter, Spare1 and Spare2 servos
int8_t                    outputMode[16]     = { 0,  0,  0,  0,  0,  1, -1, -1, -1, -1, -1, -1, -1, -1, -1, -1}; // -1 = not used, 0 = PWM, 1 = OUTPUT
uint8_t                   servoPosClosed[16] = {90, 90, 90, 90, 90, 90, 90, 90, 90, 90, 90, 90, 90, 90, 90, 90};
#else
uint8_t                   servoPosClosed[MAX_TOOLS];
#endif
double                    stepperPosClosed[MAX_TOOLS];  // V6S only

#if defined(USE_SPOOLMOTOR)
  #if defined(USE_PCA9685_SW_I2C)
    Adafruit_PWMServoDriver   motor1Pwm = Adafruit_PWMServoDriver(I2C_MOTORCTL1_ADDRESS, I2CBusMS);
    Adafruit_PWMServoDriver   motor2Pwm = Adafruit_PWMServoDriver(I2C_MOTORCTL2_ADDRESS, I2CBusMS);
    Adafruit_PWMServoDriver   motor3Pwm = Adafruit_PWMServoDriver(I2C_MOTORCTL3_ADDRESS, I2CBusMS);
  #else
    Adafruit_PWMServoDriver   motor1Pwm = Adafruit_PWMServoDriver(I2C_MOTORCTL1_ADDRESS);
    Adafruit_PWMServoDriver   motor2Pwm = Adafruit_PWMServoDriver(I2C_MOTORCTL2_ADDRESS);
    Adafruit_PWMServoDriver   motor3Pwm = Adafruit_PWMServoDriver(I2C_MOTORCTL3_ADDRESS);
  #endif
int8_t                    spoolMappings[MAX_TOOLS]      = {0, 1, 2, 3, 4, 5, 6, 7, 8, 9, 10, 11}; // tool to spool-motor mapping
uint32_t                  spoolDuration[MAX_TOOLS]      = {0, 0, 0, 0, 0, 0, 0, 0, 0, 0, 0,  0 };
bool                      spoolDirectionCCW[MAX_TOOLS]  = {true, true, true, true, true, true, true, true, true,true, true, true};
int8_t                    motorPins[][3] = {{ MA_PWM, MA_IN1, MA_IN2}, { MB_PWM, MB_IN1, MB_IN2 }, { MC_PWM, MC_IN1, MC_IN2 }, { MD_PWM, MD_IN1, MD_IN2 }, { ME_PWM, ME_IN1, ME_IN2 }};
#endif
uint8_t                   spoolMotorsFound = 0;

String                    serialBuffer0, serialBuffer1, serialBuffer2, serialBuffer3;
volatile byte             remainingSteppersFlag = 0;
volatile byte             startStepperIndex = 0;
int8_t                    toolSelections[MAX_TOOLS];
uint8_t                   remoteKey = REMOTE_NONE;
volatile uint16_t         bracketCnt = 0;
volatile uint16_t         jsonPtr = 0;
String                    jsonData;
static volatile uint16_t  intervalMask;       // bit-mask for interval reached
uint16_t                  mmsMin = 1;         // minimum moving speed for stepper in mm/s
uint16_t                  mmsMax = 800;       // maximum moving speed for stepper in mm/s
uint16_t                  speedIncrement = 5; // increment for speeds in menus
uint32_t                  pwrSaveTime;
uint32_t                  uploadStart = 0;
uint32_t                  lastEvent = 0;
volatile uint16_t         gpTimer1ms = 0;
volatile uint16_t         gpTimer20ms = 0;
volatile uint16_t         gpTimer50ms = 0;
volatile uint16_t         gpTimer100ms = 0;
static volatile unsigned  tickCounter = 0;
volatile unsigned long    lastEncoderButtonTime = 0;
volatile bool             sdRemoved = false;
volatile bool             initDone = false;   // enables sending periodical status information to serial ports
volatile bool             isPwrSave = false;
volatile bool             showMenu = false;
volatile bool             lastZEndstopState = false;
volatile bool             isIdle = false;
bool                      tmcWarning = false;
bool                      isUsingTmc = false;
bool                      isQuote = false;
bool                      isFuncKey = false;
bool                      isCtlKey = false;
bool                      ignoreQuotes = false;
volatile bool             isUpload = false;
bool                      isReceiving = false;
volatile bool             refreshingDisplay = false;
volatile uint16_t         flipDbgCnt;
volatile uint32_t         __systick = 0;        // for benchmarking only
uint32_t                  waitForDlgId = 0;
bool                      gotDlgId = false;
uint8_t                   dlgButton;
static int                lastTriggerState[4] = { -1, -1, -1, -1 };
static int                triggerStateCount[4] = { 1, 1, 1, 1 };
String                    axisNames[] = { "X", "Y", "Z", "Z2" };

volatile IntervalHandler intervalHandlers[] = {
    {  10, 0, every10ms}, 
    {  20, 0, every20ms}, 
    {  50, 0, every50ms}, 
    { 100, 0, every100ms}, 
    { 250, 0, every250ms}, 
    { 500, 0, every500ms}, 
    {1000, 0, every1s}, 
    {2000, 0, every2s}, 
    {5000, 0, every5s}
};

// forward declarations of some locally used functions
void startStepperInterval(timerVal_t duration=0);
void fncKey1();
void fncKey2();
void fncKey3();
void fncKey4();
void loopEx();

//=====================================================================================================
// Benchmarking helper functions
//=====================================================================================================
#if defined(__STM32F1XX) || defined(__STM32F4XX) || defined(__STM32G0XX)

volatile uint32_t*  debugPin = 0;
uint32_t            pinMask_Dset;
uint32_t            pinMask_Drst;
volatile bool       debugToggle = false;

void fastFlipDbg() {
  #if FASTFLIPDBG == 1
    *debugPin = (debugToggle) ? pinMask_Dset : pinMask_Drst;
  #else
    digitalWrite(DEBUG_PIN, debugToggle);
  #endif
  debugToggle = !debugToggle;
}

#define DELAY_LOOP(STPR)  for(int i=0; i < smuffConfig.stepDelay[STPR]; i++) asm("NOP");

volatile uint32_t        *stepper_reg_X = &(digitalPinToPort(X_STEP_PIN)->BSRR);
volatile uint32_t        *stepper_reg_Y = &(digitalPinToPort(Y_STEP_PIN)->BSRR);
volatile uint32_t        *stepper_reg_Z = &(digitalPinToPort(Z_STEP_PIN)->BSRR);
// preset of set/reset values to make the interrupt routine faster
uint32_t                  pinMask_Xset = digitalPinToBitMask(X_STEP_PIN);
uint32_t                  pinMask_Yset = digitalPinToBitMask(Y_STEP_PIN);
uint32_t                  pinMask_Zset = digitalPinToBitMask(Z_STEP_PIN);
uint32_t                  pinMask_Xrst = digitalPinToBitMask(X_STEP_PIN) << 16;
uint32_t                  pinMask_Yrst = digitalPinToBitMask(Y_STEP_PIN) << 16;
uint32_t                  pinMask_Zrst = digitalPinToBitMask(Z_STEP_PIN) << 16;

#endif

//=====================================================================================================
// Override functions called by ZStepper library
//=====================================================================================================

void overrideStepX(pin_t pin, bool resetPin) {
  #if defined(X_STEP_PIN_NAME)
    *stepper_reg_X = resetPin ? pinMask_Xset : pinMask_Xrst;
    #if defined(USE_XSTEP_DELAY)
      if(resetPin && smuffConfig.stepDelay[SELECTOR] > 0)
        DELAY_LOOP(SELECTOR)
    #endif
  #else
    if(!resetPin)
      STEP_HIGH_X
    else {
      STEP_LOW_X
      #if defined(USE_XSTEP_DELAY)
        if(smuffConfig.stepDelay[SELECTOR] > 0)
          delayMicroseconds(smuffConfig.stepDelay[SELECTOR]);
      #endif
    }
  #endif
}

void overrideStepY(pin_t pin, bool resetPin) {
  #if defined(Y_STEP_PIN_NAME)
    *stepper_reg_Y = resetPin ? pinMask_Yset : pinMask_Yrst;
    #if defined(USE_YSTEP_DELAY)
      if(resetPin && smuffConfig.stepDelay[REVOLVER] > 0)
        DELAY_LOOP(REVOLVER)
    #endif
  #else
    if(!resetPin)
      STEP_HIGH_Y
    else {
      STEP_LOW_Y
      #if defined(USE_YSTEP_DELAY)
        if(smuffConfig.stepDelay[REVOLVER] > 0)
          delayMicroseconds(smuffConfig.stepDelay[REVOLVER]);
      #endif
    }
  #endif
}

void overrideStepZ(pin_t pin, bool resetPin) {
  #if defined(Z_STEP_PIN_NAME)
    *stepper_reg_Z = resetPin ? pinMask_Zset : pinMask_Zrst;
    #if defined(USE_ZSTEP_DELAY)
      if(resetPin && smuffConfig.stepDelay[FEEDER] > 0)
        DELAY_LOOP(FEEDER)
    #endif
  #else
    if(!resetPin)
      STEP_HIGH_Z
    else {
      STEP_LOW_Z
      #if defined(USE_ZSTEP_DELAY)
        if(smuffConfig.stepDelay[FEEDER] > 0)
          delayMicroseconds(smuffConfig.stepDelay[FEEDER]);
      #endif
    }
  #endif
}


void endstopEventX() {
  // add your code here it you want to hook into the endstop event for the Selector
  // must be enabled by defining USE_CUSTOM_ENDSTOP_EVENT_X
}

void endstopEventY() {
  // add your code here it you want to hook into the endstop event for the Revolver
  // must be enabled by defining USE_CUSTOM_ENDSTOP_EVENT_Y
}

void endstopEventZ() {
  // add your code here it you want to hook into the 1st endstop event for the Feeder
  // must be enabled by defining USE_CUSTOM_ENDSTOP_EVENT_Z
}

void endstopEventZ2() {
  // add your code here it you want to hook into the 2nd endstop event for the Feeder
  // must be enabled by defining USE_CUSTOM_ENDSTOP_EVENT_Z2
}


//=====================================================================================================
// ISR handler functions
//=====================================================================================================

void HAL_SYSTICK_Callback(void) {
  // if(initDone) fastFlipDbg();
}

/*
  Interrupt handler for Endstops
 */

void showTriggerMessage(int axis, bool state) {

  if(state == lastTriggerState[axis]) {
    triggerStateCount[axis]++;
    return;
  }
  else {
    int index = (axis == FEEDER2) ? FEEDER : axis;
    __debugSInt(DEV3, P_EstopTriggerMsg, axisNames[axis].c_str(), String(steppers[index].getStepPositionMM()).c_str(), state, triggerStateCount[axis]);
    lastTriggerState[axis] = state;
    triggerStateCount[axis] = 1;
  }
}

void isrEndstopX() {
  bool hit = steppers[SELECTOR].evalEndstopHit(1);
  #if defined(USE_CUSTOM_ENDSTOP_EVENT_X)
    if(hit)
      endstopEventX();
  #endif
  if(smuffConfig.dbgLevel & DEV3 == DEV3)
    showTriggerMessage(SELECTOR, hit);
}

void isrEndstopY() {
  bool hit = steppers[REVOLVER].evalEndstopHit(1);
  #if defined(USE_CUSTOM_ENDSTOP_EVENT_Y)
    if(hit)
      endstopEventY();
  #endif
  if(smuffConfig.dbgLevel & DEV3 == DEV3)
    showTriggerMessage(REVOLVER, hit);
}

void isrEndstopZ() {
  bool hit = steppers[FEEDER].evalEndstopHit(1);
  #if defined(USE_CUSTOM_ENDSTOP_EVENT_Z)
    if(hit)
      endstopEventZ();
  #endif
  if(smuffConfig.dbgLevel & DEV3 == DEV3)
    showTriggerMessage(FEEDER, hit);
}

void isrEndstopZ2() {
  bool hit = false;
  #if !defined(USE_DDE)
    if(steppers[FEEDER].getEndstopPin(2) > 0) {
      hit = steppers[FEEDER].evalEndstopHit(2);
    }
  #else
    hit = steppers[DDE_FEEDER].evalEndstopHit(1);
  #endif
  #if defined(USE_CUSTOM_ENDSTOP_EVENT_Z2)
    if(hit)
      endstopEventZ2();
  #endif
  if(smuffConfig.dbgLevel & DEV3 == DEV3) {
    showTriggerMessage(FEEDER2, hit);
  }
}

/*
  Interrupt handler for StallGuard on TMC2209
 */
void isrStallDetectedX() { steppers[SELECTOR].stallDetected(); }
void isrStallDetectedY() { steppers[REVOLVER].stallDetected(); }
void isrStallDetectedZ() { steppers[FEEDER].stallDetected(); }


/*
  Interrupt handler for the LED timer
*/
void isrLedTimerHandler() {

  #if defined(USE_FASTLED_TOOLS)
    static volatile uint8_t ledTickCounter = 0;
    #if !defined(USE_MULTISERVO)
      if(!initDone || isUpload || !servoLid.isPulseComplete() || !servoCutter.isPulseComplete() || !servoWiper.isPulseComplete())
        return;
    #else
      if(!initDone || isUpload)
        return;
    #endif

    ledTickCounter++;                     // increments every 10ms
    if(ledTickCounter == 10) {            // every 100ms
      ledTickCounter = 0;
      fastLedHue++;                       // used in some color changing/fading effects
      setFastLEDStatus(fastLedStatus);
    }
    else {
      uint32_t updateTime = (uint32_t)(((fastLedStatus > FASTLED_STAT_NONE) ? smuffConfig.ledRefresh[0] : smuffConfig.ledRefresh[1])*1000);
      // update NeoPixels when the interval has been reached and no steppers are in motion
      if(remainingSteppersFlag == 0 && (micros()-lastFastLedUpdate >= updateTime)) {
        updateToolLeds();
      }
    }

  #endif
}

/*
  Interrupt handler for the servo timer.
  Available only, if MultiServo option isn't used
*/
#if defined(USE_ZSERVO) && !defined(USE_MULTISERVO)
void isrServoTimerHandler() {
  isrServoHandler();        // call servo handler
}
#endif
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
void loop() {

  // if(!firstLoop) {     // for extended debugging only
  //   __debugS(DEV3, PSTR("Looping..."));
  //   firstLoop = true;
  // }

  // Call periodical functions as the timeout has triggered.
  // Add your specific code there, if you need to have something
  // managed periodically.
  // The main loop is the better choice for dispatching, since it'll
  // allow uninterrupted serial I/O.
  for (uint8_t i = 0; i < (uint8_t)ArraySize(intervalHandlers); i++) {
    if (_BV(i) & intervalMask) {
      if(intervalHandlers[i].func != nullptr)
        intervalHandlers[i].func();
      intervalMask &= ~_BV(i);
    }
  }

#if defined(USE_SPOOLMOTOR)
  for(uint8_t i=0; i< MAX_TOOLS; i++) {
    if(spoolDuration[i] > 0) {
      if(millis() >= spoolDuration[i]) {
        stopRewindingSpool(i);
        spoolDuration[i] = 0;
      }
    }
  }
#endif

#if defined(SD_DETECT_PIN)
  // message the user if the SD-Card gets removed
  if (sdRemoved) {
    if (!sdRemovalSet) {
      userBeep();
      leoNerdBlinkRed = true;
      setFastLEDStatus(FASTLED_STAT_ERROR);
      if (isPwrSave) {
        setPwrSave(0);
      }
    }
    sdRemovalSet = true;
    if((__systick % 500) == 0) {
      char tmp[50];
      sprintf_P(tmp, P_SDCardRemoved);
      drawUserMessage(tmp);
    }
    return;
  }
  else
  {
    if (sdRemovalSet) {
      if (initSD(false)) {
        sdRemovalSet = false;
        leoNerdBlinkRed = false;
        setFastLEDStatus(FASTLED_STAT_NONE);
        lastEvent = millis();
        refreshStatus();
      }
    }
  }
#endif

  bool state = feederEndstop();
  if (state != lastZEndstopState) {
    refreshStatus();
    lastZEndstopState = state;
  }
  #if !defined(USE_SERIAL_DISPLAY)
    if(checkUserMessage()) {
      pwrSaveTime = millis();
    }
  #endif

  wasIdle = isIdle;
  isIdle = ((uint16_t)((millis() - lastEvent) / 1000) >= smuffConfig.powerSaveTimeout);
  if(isIdle != wasIdle) {
    __debugS(DEV4, PSTR("Idle switched from %d to %d"), wasIdle, isIdle);
  }

  #if !defined(USE_SERIAL_DISPLAY)
  int16_t turn;
  uint8_t button;
  bool isHeld, isClicked;

  if (!showMenu) {
    switch (remoteKey)
    {
      case REMOTE_HOME:
        remoteKey = REMOTE_NONE;
        break;
      case REMOTE_PF1:
        fncKey1();
        remoteKey = REMOTE_NONE;
        break;
      case REMOTE_PF2:
        fncKey2();
        remoteKey = REMOTE_NONE;
        break;
      case REMOTE_PF3:
        fncKey3();
        remoteKey = REMOTE_NONE;
        break;
      case REMOTE_PF4:
        fncKey4();
        remoteKey = REMOTE_NONE;
        break;
    }

    getInput(&turn, &button, &isHeld, &isClicked);
    if (isClicked || turn != 0) {
      if(isClicked && isUpload)
        resetUpload();
      if (isPwrSave) {
        setPwrSave(0);
        return;
      }
      lastEvent = millis();
    }
    #endif
    
    #if defined(USE_FASTLED_TOOLS)
    if(!isIdle) {
      if(fastLedStatus != FASTLED_STAT_NONE) {
        setFastLEDStatus(FASTLED_STAT_NONE);
        __debugS(DEV3, PSTR("FastLED status: None"));
      }
    }
    else {
      // switch on idle animation only once
      if(smuffConfig.useIdleAnimation && fastLedStatus != smuffConfig.animationType) {
        setFastLEDStatus(smuffConfig.animationType);
        __debugS(DEV3, PSTR("FastLED status: Animation"));
      }
    }
    #endif

    #if !defined(USE_SERIAL_DISPLAY)
    if ((button == MainButton && isClicked) || (button == WheelButton && isHeld)) {
      showMenu = true;
      char title[] = {"Settings"};
      showSettingsMenu(title);
      showMenu = false;
      debounceButton();
    }
    else if (button == LeftButton) {
      // applies to LeoNerd's display only
      if (isClicked) {
        fncKey1();
      }
      else if (isHeld) {
        fncKey2();
      }
    }
    else if (button == RightButton) {
      if (isClicked) {
        fncKey3();
      }
      else if (isHeld) {
        fncKey4();
      }
    }
    else if (turn != 0) {
      resetAutoClose();
      displayingUserMessage = false;
      showMenu = true;
      if (turn == -1) {
        showMainMenu();
      }
      else {
        showToolsMenu();
      }
      pwrSaveTime = millis();
      showMenu = false;
    }
  }

  if ((millis() - pwrSaveTime) / 1000 >= smuffConfig.powerSaveTimeout && !isPwrSave) {
    setPwrSave(1);
  }
  #endif

#ifdef HAS_TMC_SUPPORT
  monitorTMC(SELECTOR);
  monitorTMC(REVOLVER);
  monitorTMC(FEEDER);
#endif

  if(isTestPending) {
    isTestPending = false;
    showMenu = true;
    testRun(testToRun);
    showMenu = false;
  }
  
  loopEx();
  __flushDebug();
}

/*
* For testing only
*/
void loopEx() {

#if defined(__BRD_SKR_MINI_E3) || defined(__BRD_SKR_MINI_E3DIP)
  #if defined(USE_SW_SERIAL0)         // for testing SoftwareSerial only
    if((__systick % 2000) == 0) {     // every two seconds send string "*TG" to SW-Serial
      swSerial0.println("*TG");
    }
  #endif
  
#endif

}

void fncKey1() {
  if (strlen(smuffConfig.lButtonDown) > 0) {
    parseGcode(String(smuffConfig.lButtonDown), -1);
  }
}

void fncKey2() {
  if (strlen(smuffConfig.lButtonHold) > 0) {
    parseGcode(String(smuffConfig.lButtonHold), -1);
  }
}

void fncKey3() {
  if (strlen(smuffConfig.rButtonDown) > 0) {
    parseGcode(String(smuffConfig.rButtonDown), -1);
  }
}

void fncKey4() {
  if (strlen(smuffConfig.rButtonHold) > 0) {
    parseGcode(String(smuffConfig.rButtonHold), -1);
  }
  else {
    // open / close LID servo by default
    if (lidOpen)
      setServoLid(SERVO_CLOSED);
    else
      setServoLid(SERVO_OPEN);
  }
}

void setPwrSave(int8_t state) {
  setDisplayPowerSave(state);

  isPwrSave = state == 1;
  if (!isPwrSave) {
    pwrSaveTime = millis();
    refreshStatus();
    #if defined(USE_FASTLED_BACKLIGHT)
      setBacklightIndex(smuffConfig.backlightColor);    // turn back on backlight
    #endif
    lastEvent = millis();
  }
  else {
    #if defined(USE_FASTLED_BACKLIGHT)
      setBacklightIndex(0);                             // turn off backlight
    #endif
  }
}

bool checkUserMessage() {
  #if !defined(USE_SERIAL_DISPLAY)
    bool isClicked = getEncoderButton(true);
    if (displayingUserMessage && (isClicked || (millis() - userMessageTime > USER_MESSAGE_RESET * 1000))) {
      displayingUserMessage = false;
    }
    return displayingUserMessage;
  #else
    return false;
  #endif
}

void checkSerialPending() {
  if (Serial.available()) {
    serialEvent();
    lastEvent = millis();
  }
  if (CAN_USE_SERIAL1) {
    if (Serial1.available()) {
      serialEvent1();
      lastEvent = millis();
    }
  }
  if (CAN_USE_SERIAL2) {
    if (Serial2.available()) {
      serialEvent2();
      lastEvent = millis();
    }
  }
  if (CAN_USE_SERIAL3) {
    if (Serial3.available()) {
      serialEvent3();
      lastEvent = millis();
    }
  }
}

void resetSerialBuffer(int8_t serial) {
  switch (serial) {
  case 0:
    serialBuffer0 = "";
    break;
  case 1:
    serialBuffer1 = "";
    break;
  case 2:
    serialBuffer2 = "";
    break;
  case 3:
    serialBuffer3 = "";
    break;
  }
}
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

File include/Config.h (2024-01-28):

/**
 * SMuFF Firmware
 * Copyright (C) 2019-2024 Technik Gegg
 *
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
 */
#pragma once

#include "Pins.h"                       // path is defined in build environment of platformio.ini (-I)

#if !defined(STM32_CORE_VERSION)
typedef uint8_t     pin_t;
#else
typedef uint32_t    pin_t;
#endif

#define VERSION_STRING    "V3.25"
#define PMMU_VERSION      106               // Version number for Prusa MMU2 Emulation mode
#define PMMU_BUILD        372               // Build number for Prusa MMU2 Emulation mode
#define VERSION_DATE      "2024-01-20"
#define DEBUG_FILE        "/debug.txt"
#define DEBUG_USB         "/dbg2usb.txt"    // send debug messages to USB port (Serial 0)
#define DEBUG_EXP         "/dbg2exp.txt"    // send debug messages to EXP port (Serial 1)
#define DEBUG_OTH         "/dbg2oth.txt"    // send debug messages to other port (Serial 3)
#define CONFIG_FILE       "/SMUFF.json"
#define STEPPERS_FILE     "/STEPPERS.json"
#define MATERIALS_FILE    "/MATERIALS.json"
#define TMC_CONFIG_FILE   "/TMCDRVR.json"
#define SERVOMAP_FILE     "/SERVOMAP.json"
#define STEPPERMAP_FILE   "/REVOLVERMAP.json"
#define DATASTORE_FILE    "/EEPROM.json"
#define STARTUP_FILE      "STARTUP.DAT"
#define BEEP_FILE         "BEEP.DAT"
#define LONGBEEP_FILE     "LBEEP.DAT"
#define USERBEEP_FILE     "UBEEP.DAT"
#define ENCBEEP_FILE      "EBEEP.DAT"
#define ENCBEEPLEO_FILE   "EBEEP_LEONERD.DAT"

#define MAX_MATERIAL_LEN        5                   // max. length of materials
#define MAX_MATERIAL_NAME_LEN   10                  // max. length of material names
#define MAX_UNLOAD_COMMAND      20                  // max. length of unload command
#define MAX_WIPE_SEQUENCE       25                  // max. length of wipe sequence
#define MAX_BUTTON_LEN          15                  // max. length of button commands

#define MAX_ERR_MSG             255                 // max. length of error messages

#define NUM_STEPPERS            3
#define SELECTOR                0
#define REVOLVER                1
#define DDE_FEEDER              1
#define FEEDER                  2
#define FEEDER2                 3                   // added for boards with pre-installed stepper drivers

#define MIN_TOOLS               2
#define MAX_TOOLS               12                  // might be extended to 15

#define DSP_CONTRAST            200
#define MIN_CONTRAST            60
#define MAX_CONTRAST            250

#define I2C_SLAVE_ADDRESS       0x88        // default address if the SMuFF I2C is running in slave mode (obsolete)
#define I2C_DISPLAY_ADDRESS     0x3C        // default address for the OLED (alternative 0x3D)
#define I2C_ENCODER_ADDRESS     0x3D        // default address for the LeoNerd Encoder
#define I2C_SERVOCTL_ADDRESS    0x40        // default address for Multiservo controller
#if !defined(USE_SPOOLMOTOR_FEATHERWING)
#define I2C_MOTORCTL1_ADDRESS   0x41        // default address for 1st motor controller (Waveshare)
#define I2C_MOTORCTL2_ADDRESS   0x42        // default address for 2nd motor controller
#define I2C_MOTORCTL3_ADDRESS   0x43        // default address for 3rd motor controller
#else
#define I2C_MOTORCTL1_ADDRESS   0x61        // default address for 1st motor controller (FeatherWing)
#define I2C_MOTORCTL2_ADDRESS   0x62        // default address for 2nd motor controller
#define I2C_MOTORCTL3_ADDRESS   0x63        // default address for 3rd motor controller
#endif
#define I2C_SMUFF_WI_ADDRESS    0x45        // ESP8266 on Backbone-Board
#define I2C_EEPROM_ADDRESS      0x50        // default address for EEPROM on E3 2.0, 3.0
#define I2C_SERVOBCAST_ADDRESS  0x70        // default address for Multiservo controller (Broadcast Address)
#define I2C_PORTEX_ADDRESS      0x3F        // default address for Port extender (obsolete)
#define I2C_SPL_MUX_ADDRESS     0x3E        // default address for Splitter endstops controller

#define SERVO_WIPER         0               // output assignment on PCA9685 (Multiservo)
#define SERVO_LID           1
#define SERVO_CUTTER        2
#define SERVO_SPARE1        3
#define SERVO_SPARE2        4
#define RELAY               5
#define SERVO_USER1         6
#define SERVO_USER2         7

#define OUT1                6               // yet unused output assignment on PCA9685 (Multiservo)
#define OUT2                7
#define OUT3                8
#define OUT4                9
#define OUT5                10
#define OUT6                11
#define OUT7                12
#define OUT8                13
#define OUT9                14
#define OUT10               15

#define MOTORS_PER_CTRL     4               // number of motors controlled by one Iduino ME704 Shield
                                            // could be 5 on a custom PCB
#define MOTOR_DEFAULT_SPEED 25
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

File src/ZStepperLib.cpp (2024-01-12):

/**
 * SMuFF Firmware
 * Copyright (C) 2019-2024 Technik Gegg
 *
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
 */

 /*
  * Module implementing a stepper driver library.
  */

#include "ZStepperLib.h"

#include "Debug.h"

/**
 * @brief Default constructor. 
 * @note Not being used. Use initializing constructor instead.
*/
ZStepper::ZStepper() {
}

/**
 * @brief Initializing constructor. Creates a new instance with the given parameters. If all pins are set to 0,
 *        a "dummy" stepper is being created, which serves no other purpose than to avoid accessing uninitlialized objects.
 * 
 * @param number        The ordinal number.
 * @param descriptor    The human readable name for this instance (i.e. "Z-Axis")
 * @param stepPin       The pin on the MCU which is attached to the STEP input pin on the stepper driver.
 * @param dirPin        The pin on the MCU which is attached to the DIR input pin on the stepper driver.
 * @param enablePin     The pin on the MCU which is attached to the ENABLE input pin on the stepper driver.
 * @param acceleration  The starting acceleration value (in ticks).
 * @param maxSpeed      The maximum speed value (in ticks).
 * 
 * @note This library always uses timer ticks for speed values.
 */
ZStepper::ZStepper(int8_t number, char* descriptor, pin_t stepPin, pin_t dirPin, pin_t enablePin, int16_t acceleration, int16_t maxSpeed) {
  _number = number;
  _descriptor = descriptor;
  _stepPin = stepPin;
  _dirPin = dirPin;
  _enablePin = enablePin;
  _acceleration = acceleration;
  _maxSpeed = maxSpeed;
  if(_stepPin > 0)
    pinMode(_stepPin,    OUTPUT);
  if(_dirPin > 0)
    pinMode(_dirPin,     OUTPUT);
  if(_enablePin > 0)
    pinMode(_enablePin,  OUTPUT);
  __debugS(DEV2, PSTR("\tStepper '%-8s' stepPin: %4d   dirPin: %4d  enablePin: %4d"), _descriptor, _stepPin, _dirPin, _enablePin);
}

/**
 * @brief Default step function which takes place if no custom function has been assigned.
 * 
 * @param pin       The pin on the MCU where the STEP of the driver is attached to.
 * @param resetPin  Flag, whether to set or reset the pin.
 */
void defaultStepFunc(pin_t pin, bool resetPin) {
  if(pin == 0) 
    return;
  if(!resetPin)
    digitalWrite(pin, HIGH);
  else
    digitalWrite(pin, LOW);
}

/**
 * @brief Dumps current runtime after resetStepper() values for debugging purpose.
 * 
 */
void ZStepper::dumpParams() {
  __debugS(DEV3, PSTR("\tStepper '%-8s':"), _descriptor);
  __debugS(DEV3, PSTR("   _totalSteps:   %-6lu   _accelDist:     %-5lu   _decelPos:    %-6lu   _accelEvery: %-5ld"),
          _totalSteps, 
          _accelDistSteps, 
          _decelPos, 
          _accelEvery);
  __debugS(DEV3, PSTR("   _acceleration: %-6lu   _maxSpeed:      %-5lu   _durationInt: %-6lu   _allowAccel: %-5s"), 
          _acceleration, 
          _maxSpeed, 
          _durationInt,
          _allowAcceleration ? PSTR("Yes") : PSTR("No"));
  __debugS(DEV3, PSTR("   _intrFactor:   %-6d   _ignoreEndstop: %-5s    "), 
          _intrFactor,
          _ignoreEndstop ? PSTR("Yes") : PSTR("No"));
}

/**
 * @brief Set runtime values to default before the next movement is being executed.
 * 
 * @see prepareMovement()
 */
void ZStepper::resetStepper() {
  _durationInt = _acceleration;
  _stepCount = 0;
  _stallCount = 0;
  _intrFactor = 0;
  _intrFactorCount = 0;
  _movementDone = false;
  _endstopHit = false;
  _stallDetected = false;
  _abort = false;
  _resetSignal = false;
  dumpParams();
}

/**
 * @brief Prepares the next stepper movement by initialising runtime values.
 *        This method is the main function that needs to be called before any movement is being initiated.
 * 
 * @param steps         The number of steps to move.
 * @param ignoreEndstop Flag whether or not to ignore the endstop trigger.
 *
 */
void ZStepper::prepareMovement(long steps, bool ignoreEndstop /*= false */) {
  setDirection(steps < 0 ? CCW : CW);
  _totalSteps = abs(steps)+1;
  // calculate acceleration distance
  if(_accelDistance == 0)
    _accelDistSteps = (long)_totalSteps*0.2;  // set acceleration steps to 20% of total distance
  else
    _accelDistSteps = _accelDistance * (_endstopType == ORBITAL ? _stepsPerDegree : _stepsPerMM);

  if(_accelDistSteps > _totalSteps)
    _accelDistSteps = _totalSteps/2;
  // set deleceration to same amount of steps as the acceleration
  _decelPos = _totalSteps - _accelDistSteps;
  _accelEvery = _accelDistSteps / (_acceleration - _maxSpeed);
  _ignoreEndstop = ignoreEndstop;
  resetStepper();
}

/**
 * @brief Increment the stall count.
 * 
 */
void ZStepper::stallDetected() { _stallCount++; }

/**
 * @brief Set the descriptor of this instance.
 * 
 * @param descriptor  The human readable name for this instance.
 */
void ZStepper::setDescriptor(char* descriptor) { _descriptor = descriptor; }

/**
 * @brief Get the descriptor of this instance.
 * 
 * @returns The currently set human readable name of this instance.
 */
char* ZStepper::getDescriptor() { return _descriptor; }

/**
 * @brief Sets the moving direction.
 * 
 * @param direction   The direction (CW or CCW) in that the stepper motor shall move.
 * 
 * @see MoveDirection enumeration
 */
void ZStepper::setDirection(ZStepper::MoveDirection direction) {
  if(_dirPin != 0) {
    _dir = direction;
    uint32_t val = !_invertDir ? (_dir == CCW ? HIGH : LOW) : (_dir == CCW ? LOW : HIGH);
    digitalWrite(_dirPin, val);
    __debugS(DEV2, PSTR("\tStepper '%-8s' direction: %s"), _descriptor, _dir==CW ? "CW" : "CCW");
  }
}
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

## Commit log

2019-05-22 Recent changes
    [SMUFF.CFG]
2019-05-22 Wiring image added
2019-05-23 Added Prusa MMU2 emulation mode
    [SMUFF.CFG]
2019-05-23 Added EmulatePrusa flag
    [SMUFF.CFG]
2019-09-11 Modifications for new platform and better Prusa Emulation Mode
    [SMUFF.CFG]
2019-09-11 Bugfixes from last checkin
    [Config.cpp, Config.h, DataStore.cpp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]
2019-09-23 Latest version. See README.MD
    [SKR mini LCD board.kicad_pcb, SKR mini LCD board.sch, SMUFF_Duet.CFG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]
2019-09-27 Some minor improvements
    [SMUFF_Duet.CFG, SMUFF_PMMU.CFG]
2019-09-27 Bugfix for Arduino
2019-10-03 Some bugfixes and adjustments for the SKR board
    [SMUFF_Duet.CFG, SMUFF_PMMU.CFG]
2019-10-11 Software enhancements
    [SMUFF_Duet.CFG, SMUFF_PMMU.CFG]
2019-10-13 Exchanged some parameters for the SKR config
    [SMUFF_Duet.CFG, SMUFF_PMMU.CFG]
2019-10-23 Updated to version 1.63
    [SMUFF_Duet.CFG, SMUFF_PMMU.CFG]
2019-11-08 Updated to 1.64 for servo use as replacement for the Revolver
    [SMUFF_Duet.CFG, SMUFF_PMMU.CFG]
2019-11-10 Added Servo settings to CFG files
    [SMUFF_Duet.CFG, SMUFF_PMMU.CFG]
2019-11-10 Bugfix - hangs in "busy" after startup due to waiting for the Revolver endstop
    [Config.h, SMuFFtools.cpp]
2019-12-10 Updated Servo connection
2019-12-10 Fixed compiler errors/warnings for Wanhao i3
    [Config.h, GCodes.cpp, Menus.cpp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]
2019-12-14 Marked the WS2812 as optional
    [SKR mini LCD board.sch]
2019-12-29 Added CFG file for servo variant (PMMU as base)
    [SMUFF_Servo.CFG]
2019-12-29 Added CFG for servo variant on Duet
    [SMUFF_Servo_Duet.CFG]
2019-12-29 Bugfix for Duet3D mode on SKR mini
    [Config.h, SMuFFtools.cpp]
2020-05-03 New version for preview. Added ESP32 custom board.
    [SKR mini LCD board.kicad_pcb, SKR mini LCD board.sch, SMUFF_Servo.CFG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]
2020-05-12 Added code for PCF8574 port expander on ESP32
    [ESP32 Controller.kicad_pcb, ESP32 Controller.sch]
2020-05-12 Added ESP32 Controller PDF / cleanup
2020-05-13 Modified Servo handling on SKR (STM32)
    [SMUFF_Duet.CFG, SMUFF_PMMU.CFG, SMUFF_Servo.CFG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]
2020-05-18 Added more support for SMuFF V5
    [SMUFF_Duet.CFG, SMUFF_PMMU.CFG, SMUFF_Servo.CFG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]
2020-05-22 Updates and bug fixes
    [Config.h, SMuFF.cpp, SMuFF.h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]
2020-06-04 Add support for FYSETC AIOII
    [SMUFF_Duet.CFG, SMUFF_PMMU.CFG, SMUFF_Servo.CFG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]
2020-06-07 Bugfix for MMU emulation mode 'start' cmd
    [SimpleGCodeParser.cpp]
2020-06-07 Added ServoCycles for each servo to config
2020-06-07 Added ServoCycles for each servo in config
2020-06-08 Added WipeSequence to SMuFF.CFG
    [SMUFF_Duet.CFG, SMUFF_PMMU.CFG, SMUFF_Servo.CFG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]
2020-06-22 Updated Pins.h for STM32
2020-06-24 Moved to FastLED-STM32 library
2020-06-26 Added new menu for "Display" settings
    [SMUFF_Duet.CFG, SMUFF_PMMU.CFG, SMUFF_Servo.CFG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]
2020-07-12 Bugfix for PMMU mode
    [Config.h, SMuFF.cpp]
2020-07-12 Added SOFTRESET option to some builds (for Marlin MMU mode)
2020-07-12 Added MARLIN2_ONLY build flag
2020-08-24 A lot of changes for 2.10 (see README.md)
    [SKR mini E3 LCD board.sch, SKR mini LCD board.sch, SMUFF_Duet.CFG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]
2020-09-02 Bugfixing / TMC2209 optimization
    [Config.cpp, Config.h, DataStore.cpp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]
2020-09-03 Moved servo on Y-Stepper for E3-DIP
2020-11-03 Mostly refactoring (see README for details)
    [SERVOMAP.CFG.json]
2020-11-25 Bug fixing (see README.MD)
    [Config.cpp, Config.h, Led.cpp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]
2020-12-06 Updated for .mnu and .opt files
    [Relay-Board.kicad_pcb, Relay-Board.sch]
2020-12-08 Update to make the FW STM32 V10.0.1 compliant (see README.md)
    [Relay-Board.kicad_pcb, Relay-Board.sch, Relay-Board.step]
2020-12-08 Relay-Board schematics added
2020-12-09 Updated Relay-Board PCB
    [Relay-Board-B_Cu.gbr, Relay-Board-B_Mask.gbr, Relay-Board-B_Paste.gbr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]
2020-12-20 SKR E3 V2.0 bug fixing
    [Config.h, Pins.h, SMuFF.cpp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]
2021-02-16 ESP32 HAL
2021-02-16 Compilable ESP32 firmware
2021-02-16 STM32 HAL
    Add STM32 HAL and reduce ram footprint
2021-02-16 Fix i2c missing common defines
    [ClickEncoder.h, SMuFF.h, SetupInit.cpp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]
2021-02-22 Minor bug fixes, see README.md
    [Config.cpp, Config.h, DataStore.cpp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]
2021-03-02 Bug fixes and minor changes
    [SERVOMAP.CFG.json]
2021-03-16 See README.md
    [SERVOMAP.json]
2021-03-22 Add Leonerd soft i2c support
2021-03-23 Fix case in include
2021-03-23 Revert release unused resources
    [Pins.h]
2021-03-25 Bug fixes / SW I2C integration
    [Config.h, GCodes.cpp, Led.cpp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]
2021-03-25 Corrected wrong init of Wire
2021-05-19 Bug Fixing for WebInterface
    [Config.cpp, Config.h, GCodes.cpp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]
2021-07-13 Mods for DDE / added STL files
    [20x20-Extrusion-Mount.stl, Base-Left-Cable-Cover.stl, Base-Left-Gear-Cover.stl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]
2021-08-11 Update to 2.33 (see README.md)
    [Relay-Board-BOM.csv]
2021-09-24 code reorganization and bug fixing for 2.40
    [Config.cpp, Config.h, GCodes.cpp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]
2021-09-24 cleanup for schematics
2021-11-28 Renamed folder to avoid confusion
    [Pins.h]
2021-11-28 Added RET6 MCU option for V2.0 boards
2021-12-06 added new STLs
    [Servo-Small-Carrier.stl, Servo-Small-Horn.stl, Servo-Small-Lever.stl]
2022-04-20 Initial commit for V3
    [Housing SKR New-GoPro-Mount.stl, Housing SKR New-Lid-BTT24.stl, Housing SKR New-Lid-DIY.stl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]
2022-04-29 Added missing _DDE option for E3 V1.2
    [Dupont-5x2-key.stl]
2022-05-19 Bug fixes and minor updates; see README
    [Config.cpp, Config.h, DataStore.cpp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]
2022-05-21 Bugfix hanging at startup when debug.txt is missing
    [Config.cpp]
2022-06-17 Updated to V3.12; See README.md
    [Relay-Board.kicad_pcb, Relay-Board.kicad_sch, SERVOMAP.json]
2022-07-25 Updated to V3.13; See README.md
    [SMuFF-Backbone.kicad_pcb, SMuFF-Backbone.kicad_sch]
2023-02-03 Bug fix, see Readme
    [Config.h, SMuFFtools.cpp, SetupInit.cpp]
2023-02-14 Bug fixes for DDE configuration, see Readme.md
    [Config.h, GCodes.cpp, SMuFF.h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]
2023-03-13 Updated to 3.16, see README.md
    [Relay-Board-bottom-pos.csv, Relay-Board-top-pos.csv]
2023-03-16 Updated for arduino framework 2.4.0
    [Relay-Board.kicad_pcb, Relay-Board.kicad_sch]
2023-03-28 Added new Connector/NeoPixel PCBs and parts
    [Base-Left-Strain-Relief.stl, Connector-PCB-Mount.stl, Connector-PCB-Top-Cover.stl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]
2023-04-02 Updated Base-Left STL
2023-05-29 Updated to 3.18, fixed display bug in menus
    [Config.h, DisplayTools.cpp, SMuFFtools.cpp]
2023-06-13 Updated to 3.19, fixed bug in Selector homing
    [Config.h, ZStepperLib.cpp]
2023-12-22 bugfix, Motorized Spool Rewinder option added
    [Config.cpp, Config.h, GCodes.cpp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]
2024-02-01 Updated platform and framework to latest releases

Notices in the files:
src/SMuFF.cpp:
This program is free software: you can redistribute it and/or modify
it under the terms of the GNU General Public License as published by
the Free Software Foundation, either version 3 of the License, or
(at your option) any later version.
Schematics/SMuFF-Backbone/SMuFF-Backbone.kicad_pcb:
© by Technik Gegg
